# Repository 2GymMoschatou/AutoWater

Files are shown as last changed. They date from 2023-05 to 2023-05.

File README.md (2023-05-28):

# AutoWater
Σύστημα αυτόματου ποτίσματος τροφοδοτούμενου από δεξαμενή συλλογής νερού

Σχεδίαση, προγραμματισμός και κατασκευή μοντέλου επίδειξης ενός συστήματος αυτόματου ποτίσματος τροφοδοτούμενου από δεξαμενή συλλογής του νερού της βροχής.
Το σύστημα ανιχνεύει την υγρασία του εδάφους σε δύο σημεία (παρτέρια) και ανάλογα με το ποσοστό υγρασίας ποτίζει το ένα ή και τα δύο σημεία, ανεξάρτητα μεταξύ τους. Η διαδικασία του ποτίσματος πραγματοποιείται κατά τις βραδινές ώρες για να είναι πιο αποδοτική.
Το νερό για το πότισμα προέρχεται από δεξαμενή συγκέντρωσης των νερών της βροχής, η οποία ελέγχεται από αισθητήρα στάθμης του νερού. Αν η δεξαμενή είναι άδεια τα παρτέρια ποτίζονται από το δίκτυο ύδρευσης.
Η κατάσταση του συστήματος, καθώς και οι μετρήσεις υγρασίας και θερμοκρασίας του περιβάλλοντος προβάλλονται μέσω της θύρας USB σε υπολογιστή.

Υλικά και κόστος του συστήματος αυτόματου ποτίσματος
| Περιγραφή | Κόστος |
| --- | --- |
| Arduino Uno (συμβατό) | 9,90 € |
| Φωτοαντίσταση |	0,20 € |
| Αντίσταση 10ΚΩ | 0,02 € |
| Αισθητήρας υγρασίας εδάφους (2 τεμ) | 3,80 € |
| Αισθητήρας υπερήχων HC-SR04 |	2,50 € |
| Αισθητήρας υγρασίας και θερμοκρασίας DHT11 | 2,40 € |
| Servo Micro MG90 (3 τεμ) | 14,70 € |
| Αντλία υγρών 5V (2 τεμ) |	9,80 € |
| Σωλήνας σιλικόνης (6x8mm) 2μ | 2,40 € |
| Μονάδες ρελέ (2 τεμ) | 3,80 € |
| Μπαταριοθήκη 4ΑΑ | 0,60 € |
| Μπαταρίες ΑΑ (4 τεμ) | 1,80 € |
| Διακόπτης ON-ON | 0,80 € |
| Διάτρητη πλακέτα σε σχήμα breadboard | 3,80 € |
| Σύνολο | 56,52 € |

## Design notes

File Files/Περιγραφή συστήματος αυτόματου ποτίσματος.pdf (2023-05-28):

# Σύστημα αυτόματου ποτίσματος τροφοδοτούμενου από δεξαμενή συλλογής νερού

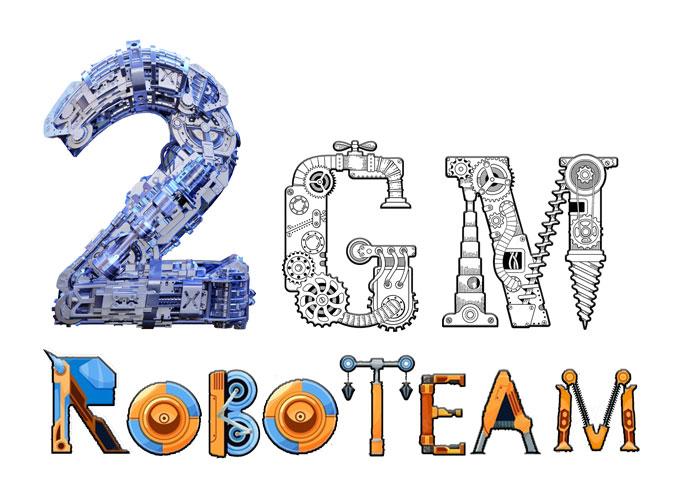
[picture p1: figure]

# 2ο Γυμνάσιο Μοσχάτου

# Σχολικό έτος 2022 - 23

## Η κατανομή των υδατικών πόρων στην Ελλάδα

Η χώρα μας διαθέτει συνολικά επαρκείς υδατικούς πόρους, επιφανειακούς και υπόγειους, αλλά η γεωμορφολογική της σύνθεση, η γεωλογική δομή, η άνιση κατανομή των βροχοπτώσεων στο χώρο και στο χρόνο και τέλος η άνιση κατανομή των δραστηριοτήτων, και επομένως των υδατικών αναγκών, κυρίως στο χώρο, μειώνουν σημαντικά τη διαθέσιμη ποσότητα και δυσκολεύουν την αξιοποίηση.
Τα ιδιαίτερα χαρακτηριστικά της χώρας, σε σχέση με τους υδατικούς πόρους, από τα οποία προκύπτουν και οι δυσκολίες διαχείρισής τους, μπορούν να ταξινομηθούν ως εξής :
- Ως προς την κατανομή των βροχοπτώσεων, η οποία είναι άνιση ως προς το χώρο και το χρόνο. Συγκεκριμένα η Δυτική Ελλάδα δέχεται μεγαλύτερα ύψη βροχών από ότι η Ανατολική.
- Ως προς την κατανομή της ζήτησης, η οποία είναι άνιση ως προς το χώρο και ως προς το χρόνο.
- Ως προς τη μορφολογία της επιφάνειας της χώρας, με τη δημιουργία πολλών μικρών υδάτινων ρευμάτων.
Σχετικά με την κατανομή των βροχών παρατηρούνται σημαντικές διαφοροποιήσεις από περιοχή σε περιοχή. Έτσι, στα νότια και τα νησιά το φθινόπωρο και το χειμώνα έχουμε το μέγιστο της βροχής, ενώ το καλοκαίρι και μέρος της άνοιξης επικρατεί σχεδόν ξηρασία. Στα βόρεια η χρονική αυτή κατανομή αλλάζει σημαντικά, όπου φθινόπωρο-χειμώνας-άνοιξη έχουν σχεδόν ισοκατανομή της βροχής, με το καλοκαίρι να παραμένει σχεδόν ξερό. Είναι φυσικό, ότι κάτω από αυτές τις συνθήκες, για να γίνει δυνατή η ανάπτυξη των καλλιεργειών από τα μέσα της άνοιξης μέχρι το τέλος τουλάχιστον του καλοκαιριού, χρειάζεται η εφαρμογή αρδεύσεων.

## Περιγραφή του συστήματος αυτόματου ποτίσματος

Παραδοσιακά σε περιοχές που
παρατηρείται μεγαλύτερη ξηρασία οι
κάτοικοι συγκέντρωναν το νερό της
βροχής σε στέρνες, όπως μας μαρτυρούν και λογοτεχνικές πηγές. Στο σύστημα αυτόματου ποτίσματος που σχεδιάσαμε συγκεντρώνουμε το νερό της βροχής σε δεξαμενή, από όπου ποτίζουμε τα φυτά που βρίσκονται σε δύο διαφορετικά παρτέρια.
Το σύστημά μας, ανιχνεύει την υγρασία του εδάφους σε δύο σημεία και ανάλογα με το ποσοστό υγρασίας ενεργοποιεί τις αντίστοιχες αντλίες για να τα ποτίσει. Η διαδικασία του ποτίσματος πραγματοποιείται τις βραδινές ώρες για να έχουμε μικρότερη εξάτμιση, επομένως να είναι πιο αποδοτική. Αν η δεξαμενή είναι
άδεια τα παρτέρια ποτίζονται από το
δίκτυο ύδρευσης.

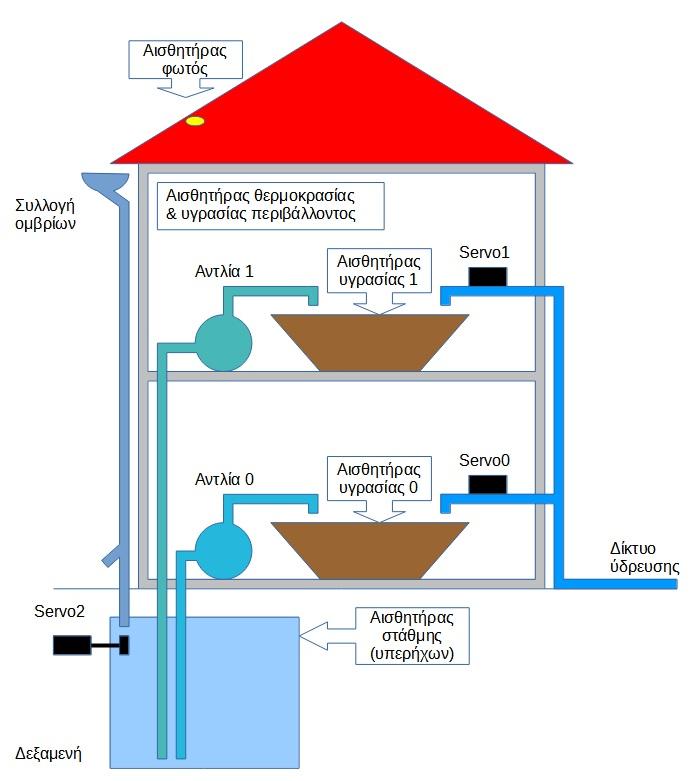
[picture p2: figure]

Για την προσομοίωση της λειτουργίας και του προγραμματισμού των επιμέρους στοιχείων, καθώς και του πλήρους συστήματος, πριν την τελική συναρμολόγηση, χρησιμοποιήθηκε το ελεύθερο λογισμικό TinkerCAD. Στο παρακάτω σχέδιο βλέπουμε το κύκλωμα, με το οποίο έγινε η προσομοίωση στο TinkerCAD.

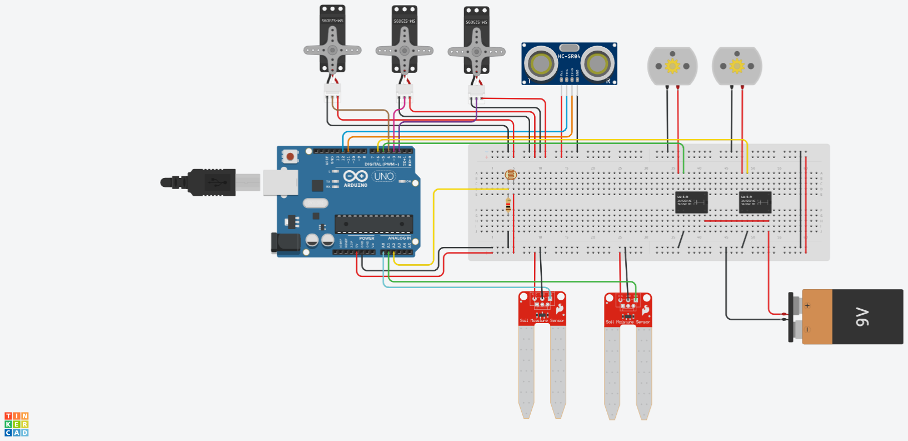
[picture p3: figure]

Στην τελική υλοποίηση τοποθετήθηκαν μονάδες ρελέ στη θέση των ρελέ που φαίνονται στο σχέδιο και ο αισθητήρας DHT11, τα οποία δεν υπάρχουν στο λογισμικό της προσομοίωσης.

Για την κατασκευή του συστήματος χρησιμοποιήσαμε:
Περιγραφή | Τεμάχια | Τιμή μονάδας | Κόστος
Arduino Uno SMD Compatible - CH340 | 1 | 9.90 € | 9.90 €
Φωτοαντίσταση LDR 5mm | 1 | 0.20 € | 0.20 €
Αντίσταση 10ΚΩ | 1 | 0,02 € | 0,02 €
Αισθητήρα υγρασίας εδάφους | 2 | 1,90 € | 3,80 €
Αισθητήρα υπερήχων HC-SR04 | 1 | 2.50 € | 2.50 €
Αισθητήρα υγρασίας και θερμοκρασίας DHT11 | 1 | 2,40 € | 2,40 €
Servo micro MG90S | 3 | 4,90 € | 14,70 €
Αντλίες υγρών 5V | 2 | 4,90 € | 9,80 €
Σωλήνας σιλικόνης (6x8mm) μ | 2 | 1,20 € | 2,40 €
Relay module - 1 channel 5V high level trigger | 2 | 1.90 € | 3,80 €
Μπαταριοθήκη 4ΑΑ με καλώδια | 1 | 0,60 € | 0,60 €
Μπαταρίες ΑΑ (4τεμ) | 1 | 1,80 € | 1,80 €
Διακόπτης ON-ON | 1 | 0,80 € | 0,80 €
Διάτρητη πλακέτα σε σχήμα breadboard | 1 | 3,80 € | 3,80 €
Συνολικό κόστος | | | 56,52 €
Στον παραπάνω πίνακα δεν περιλαμβάνεται το κόστος της καλωδίωσης, το οποίο εξαρτάται από το μέγεθος της μακέτας που θα κατασκευαστεί.

## Κατασκευή του μοντέλου επίδειξης

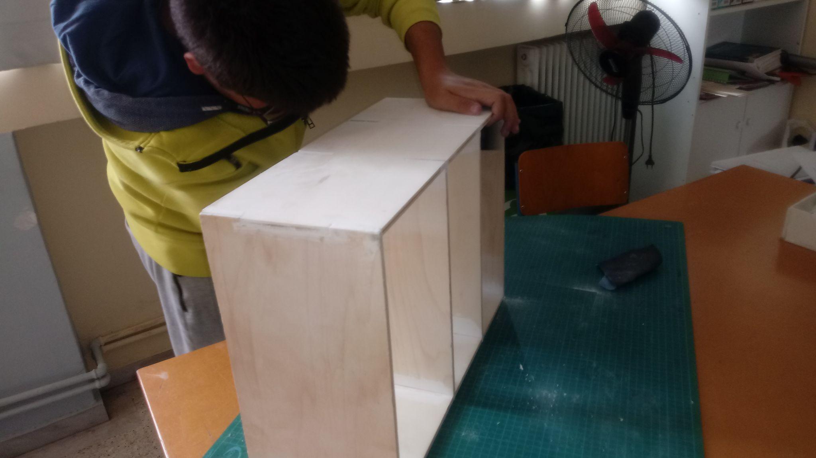
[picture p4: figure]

Για την επίδειξη της λειτουργίας του
συστήματος κατασκευάσαμε ένα ξύλινο
ομοίωμα σπιτιού με υπόγειο, ισόγειο και
πρώτο όροφο. Το ομοίωμα βάφτηκε με λευκό χρώμα στους δύο ορόφους και γκρι στο υπόγειο.

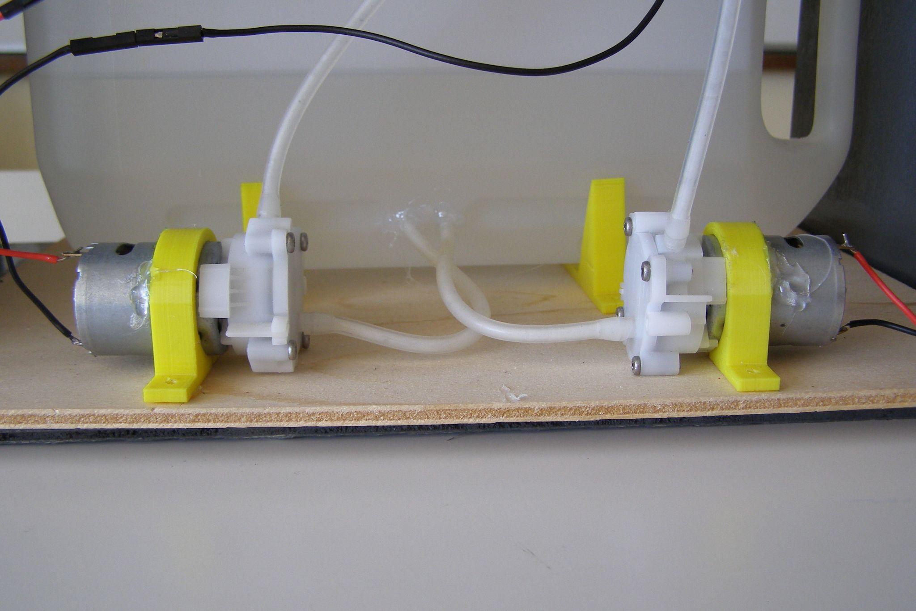
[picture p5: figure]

Στο υπόγειο του κτιρίου τοποθετήσαμε τις αντλίες του συστήματος και ένα πλαστικό δοχείο για δεξαμενή, στο οποίο ανοίξαμε τις υποδοχές για τις απαραίτητες σωληνώσεις.

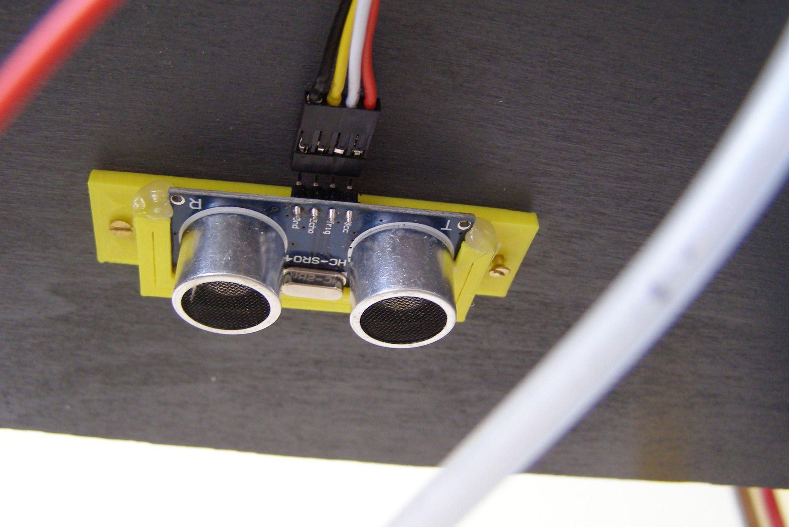
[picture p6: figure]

Ο αισθητήρας υπερήχων τοποθετήθηκε στην οροφή του υπογείου και ανιχνεύει το ύψος του νερού της δεξαμενής από το αντίστοιχο άνοιγμα στο δοχείο.

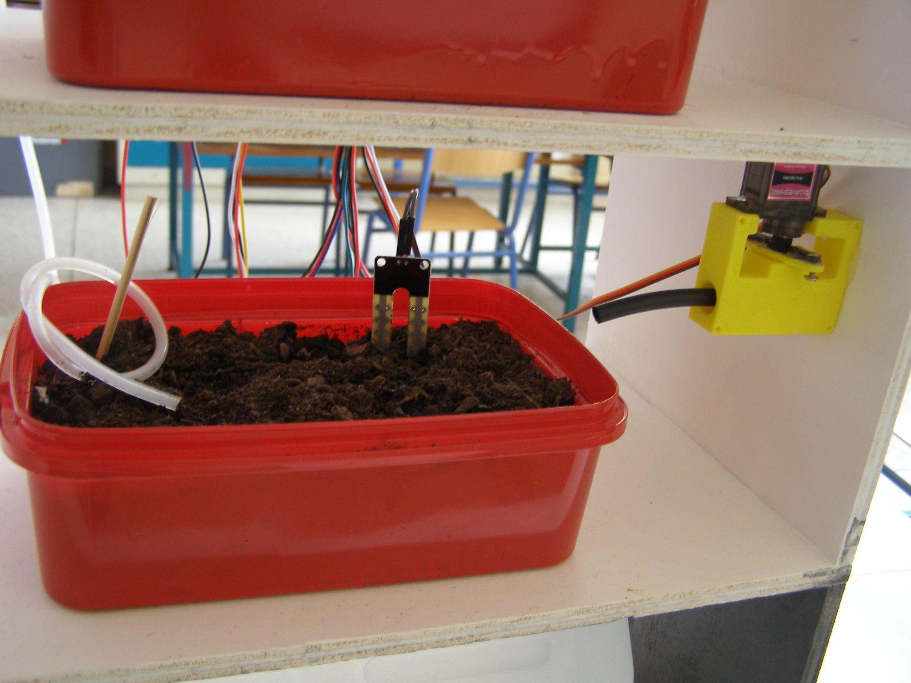
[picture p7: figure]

Στους ορόφους του κτιρίου τοποθετήσαμε πλαστικά δοχεία με χώμα για τα παρτέρια, όπου βάλαμε τους αισθητήρες υγρασίας εδάφους. Σε κάθε όροφο έχουμε και ένα διακόπτη για το νερό του δικτύου ύδρευσης ελεγχόμενο από servo.

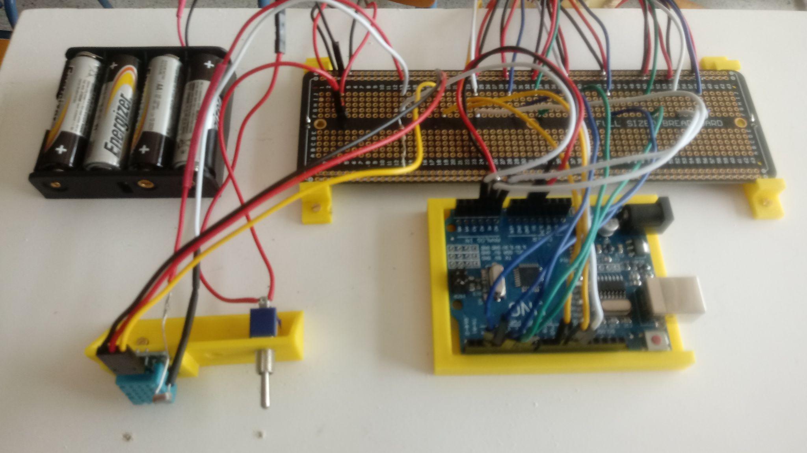
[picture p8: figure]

Στο πάνω μέρος του ομοιώματος τοποθετήσαμε την πλακέτα του Arduino Uno και την πλακέτα στην οποία καταλήγουν όλες οι καλωδιώσεις του συστήματος. Επίσης, τοποθετήσαμε τον αισθητήρα θερμοκρασίας-υγρασίας, τη φωτοαντίσταση και τις μπαταρίες τροφοδοσίας των αντλιών με το διακόπτη τους

Η σκεπή του ομοιώματος κατασκευάστηκε από διαφανές plexiglass.

Στο εξωτερικό μέρος τοποθετήθηκε ομοίωμα της υδρορροής με ένα διακόπτη ελεγχόμενο από servo για τον έλεγχο της παροχής νερού στη δεξαμενή.

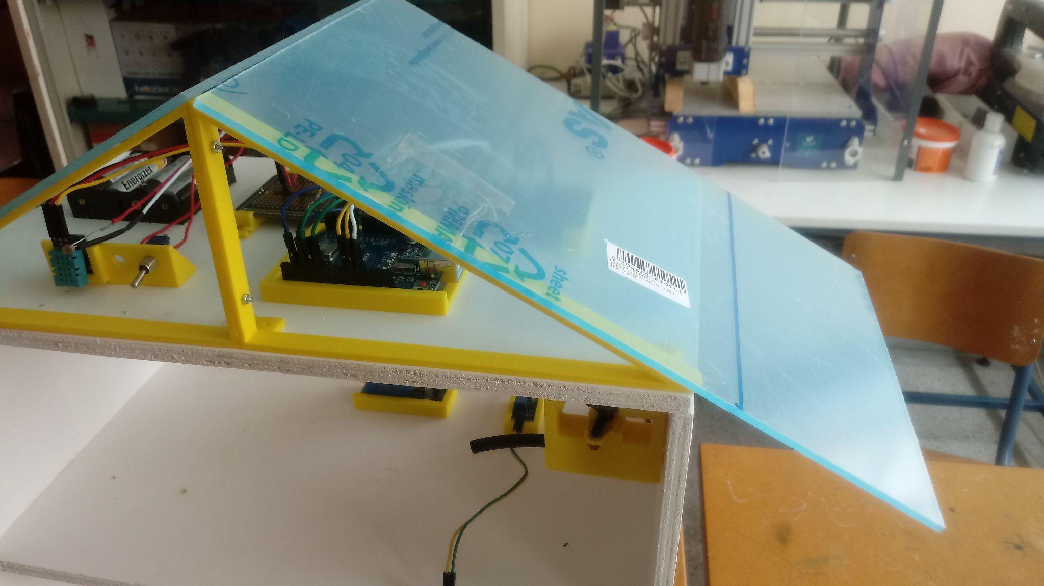
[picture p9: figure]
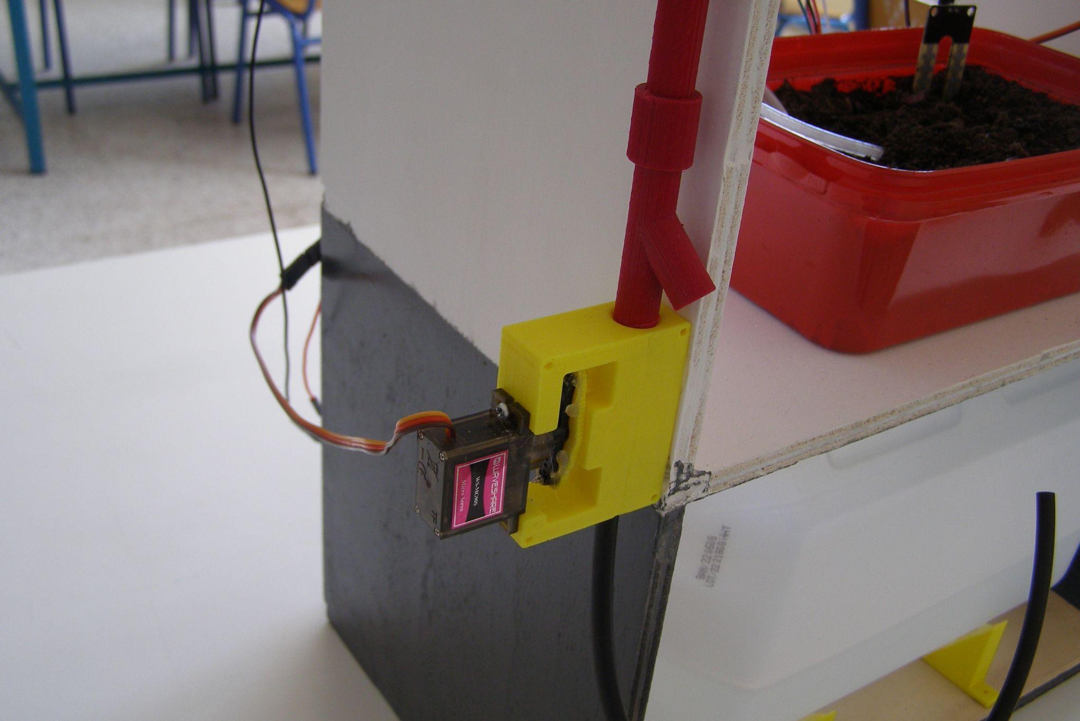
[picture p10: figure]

Οι βάσεις για τους αισθητήρες και τα υπόλοιπα στοιχεία του συστήματος, καθώς και η βάση της στέγης και η υδρορροή, σχεδιάστηκαν με το πρόγραμμα TinkerCAD και εκτυπώθηκαν με τον 3D printer, ενώ για τους διακόπτες νερού χρησιμοποιήθηκε ελεύθερο σχέδιο από την ιστοσελίδα Thingiverse.com (https://www.thingiverse.com/thing:1624066).
Η μακέτα του συστήματος ολοκληρωμένη
φαίνεται στην παρακάτω φωτογραφία.

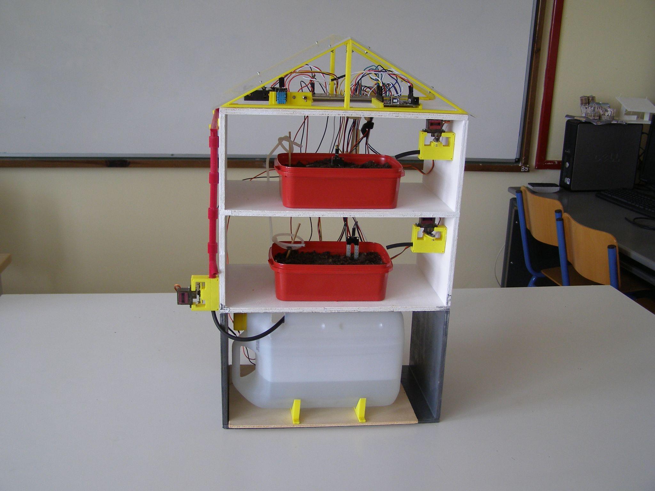
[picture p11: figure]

## Προγραμματισμός του συστήματος αυτόματου ποτίσματος

Για τον προγραμματισμό του συστήματος χρησιμοποιήθηκε το λογισμικό Arduino IDE.
Ένα απλό πρόγραμμα που επαναλαμβάνεται στο Arduino αποτελείται από δύο συναρτήσεις: •Τη συνάρτηση setup(), που εκτελείται μόνο μια φορά στην αρχή του προγράμματος, και καθορίζει τις αρχικές ρυθμίσεις του συστήματος.
•Τη συνάρτηση loop(), που περιέχει τον κυρίως κώδικα του προγράμματός μας, και εκτελείται κυκλικά μέχρι την απενεργοποίηση ή την επανεκκίνηση του Arduino.

Στο πρώτο μέρος του προγράμματός μας εισάγουμε τις απαραίτητες βιβλιοθήκες για την εκτέλεσή του και δημιουργούμε τα αντικείμενα των servo που χρειαζόμαστε, ορίζοντας και τις αρχικές τους θέσεις.

//Including libraries
#include <Servo.h>

#include <DHT.h>

//Creating servos and setting initial positions Servo servo0;
Servo servo1;
Servo servo2;
int servo0Pos = 90;
int servo1Pos = 90;
int servo2Pos = 0;

Έπειτα ορίζουμε τους ακροδέκτες όπου θα συνδεθούν τα servo, τα ρελέ και οι αισθητήρες του κυκλώματος.

//Setting pins
const int servo0Pin=2;
const int servo1Pin=3;
const int servo2Pin=4;
const int relay0Pin=5;
const int relay1Pin=6;
const int dhtPin=10;
const int echoPin=11;
const int trigPin=12;
const int hygro0Pin=A0;
const int hygro1Pin=A1;
const int lightPin=A2;

Επίσης ορίζουμε το όνομα και τον τύπο των μεταβλητών, καθώς και τον τύπο του αισθητήρα DHT που θα χρησιμοποιήσουμε.

//Setting the variables
int hygro0;
int hygro1;
int light;

long duration;
long distance;
bool water0;
bool water1;
float hum;
float temp;

//Setting the DHT sensor type
#define dhtType DHT11

DHT dht(dhtPin, dhtType);

Τέλος καθορίζουμε τις τιμές των μεταβλητών, όπου θα λαμβάνονται οι κρίσιμες αποφάσεις, ώστε, σε περίπτωση αλλαγής των ορίων λειτουργίας της δεξαμενής για παράδειγμα, να τροποποιούνται οι τιμές μόνο μια φορά και όχι σε όποιο σημείο του προγράμματος πρέπει να πάρουμε μια απόφαση.

//Setting the critical values
const int minDistance=5;
const int maxDistance=10;
const int minLight=15;

Στην ενότητα setup, πρώτα ενεργοποιούμε την σειριακή θύρα του Arduino και τον αισθητήρα υγρασίας-θερμοκρασίας DHT11. Στη συνέχεια συνδέουμε τα Servo με τους αντίστοιχους ακροδέκτες και τα τοποθετούμε στην αρχική τους θέση. Τέλος καθορίζουμε τον τρόπο λειτουργίας των ψηφιακών ακροδεκτών που έχουμε ορίσει ότι θα χρησιμοποιήσουμε.

void setup() {
//Initialize serial communication and DHT sensor
Serial.begin(9600);
dht.begin();

//Attaching servos and writing initial positions servo0.attach(servo0Pin);
servo1.attach(servo1Pin);
servo2.attach(servo2Pin);
servo0.write(servo0Pos);
servo1.write(servo1Pos);
servo2.write(servo2Pos);

//Initialize digital pins
pinMode(relay0Pin, OUTPUT); pinMode(relay1Pin, OUTPUT); pinMode(trigPin, OUTPUT);
pinMode(echoPin, INPUT);

}

Στην ενότητα loop ξεκινάμε με την ανάγνωση των ενδείξεων από τους αισθητήρες του συστήματος, δηλαδή το ύψος της δεξαμενής νερού, την υγρασία του εδάφους στα παρτέρια και την φωτεινότητα.

void loop() {
//Read water level with ultrasonic sensor
digitalWrite(trigPin, LOW); delayMicroseconds(2);
digitalWrite(trigPin, HIGH); delayMicroseconds(10);
digitalWrite(trigPin, LOW); duration = pulseIn(echoPin, HIGH); distance = (duration/2) / 29.1; delay(100);

//Read moisture of plants at floor 0 hygro0 = analogRead(hygro0Pin); hygro0 = constrain(hygro0,400,1023); hygro0 = map(hygro0,400,1023,100,0); delay(100);

//Read moisture of plants at floor 1 hygro1 = analogRead(hygro1Pin); hygro1 = constrain(hygro1,400,1023); hygro1 = map(hygro1,400,1023,100,0); delay(100);

//Read light
light = analogRead(lightPin);
delay(100);

//Reading environment temperature and humidity
//Reading temperature or humidity takes about 250 milliseconds! hum = dht.readHumidity();
temp = dht.readTemperature();
delay(250);

Ελέγχουμε στη συνέχεια το ύψος του νερού στη δεξαμενή και, στην περίπτωση που ανιχνεύσουμε το ελάχιστο όριο που έχουμε θέσει, διακόπτουμε την παροχή νερού από την υδρορροή, για να αποφύγουμε την υπερχείλιση της δεξαμενής.

//Check tank overflow
if (distance<=minDistance){
servo2Pos=90;
servo2.write(servo2Pos);
delay(100);
}
else{

servo2Pos=0;
servo2.write(servo2Pos);
delay(100);
}

Μετά ελέγχουμε την υγρασία του πρώτου παρτεριού και καθορίζουμε αν τα φυτά χρειάζονται πότισμα.

//Check plants in floor 0
if (light<minLight){
if (hygro0<30){
water0=true;
}
}
if (hygro0>90){
water0=false;
}

Αν τα φυτά μας πρέπει να ποτιστούν, ελέγχουμε αν η δεξαμενή έχει νερό και ενεργοποιούμε την αντίστοιχη αντλία. Στην περίπτωση που η δεξαμενή δεν έχει νερό ανοίγουμε το δίκτυο ύδρευσης.

//Watering plants in floor 0
if (water0==true){
if (distance<maxDistance){ digitalWrite(relay0Pin, HIGH); delay(100);
servo0Pos=90;
servo0.write(servo0Pos);
delay(100);
}
else{
digitalWrite(relay0Pin, LOW); delay(100);
servo0Pos=0;
servo0.write(servo0Pos);
delay(100);
}
}

Επαναλαμβάνουμε τη ίδια διαδικασία και για το δεύτερο παρτέρι.

//Check plants in floor 1
if (light<minLight){
if (hygro1<30){
water1=true;
}
}

if (hygro1>90){
water1=false;
}

//Watering plants in floor 1
if (water1==true){
if (distance<maxDistance){ digitalWrite(relay1Pin, HIGH); delay(100);
servo1Pos=90;
servo1.write(servo1Pos);
delay(100);
}
else{
digitalWrite(relay1Pin, LOW); delay(100);
servo1Pos=0;
servo1.write(servo1Pos);
delay(100);
}
}

Όταν η υγρασία του εδάφους φτάσει στην τιμή που έχουμε καθορίσει, τότε το πότισμα στο αντίστοιχο παρτέρι διακόπτεται.

//Stop watering in floor 0
if (water0==false){
digitalWrite(relay0Pin, LOW); delay(100);
servo0Pos=90;
servo0.write(servo0Pos);
delay(100);
}

//Stop watering in floor 1
if (water1==false){
digitalWrite(relay1Pin, LOW); delay(100);
servo1Pos=90;
servo1.write(servo1Pos);
delay(100);
}

Στο τέλος της ενότητας οι ενδείξεις των αισθητήρων διαβιβάζονται στον συνδεδεμένο υπολογιστή μέσω της σειριακής θύρας του Arduino.

//Print out the values
Serial.print("Water depth ");

Serial.print(distance);
Serial.println(" cm");
Serial.print("Soil humidity 0: "); Serial.print(hygro0);
Serial.println("%");
Serial.print("Soil humidity 1: "); Serial.print(hygro1);
Serial.println("%");
Serial.print("Light: ");
Serial.println(light);
Serial.print("Environment Humidity: "); Serial.print(hum);
Serial.println("%");
Serial.print("Environment Temperature: ");
Serial.print(temp);
Serial.println("°C ");

Ακολουθεί μια παύση ενός δευτερολέπτου για το κλείσιμο της ενότητας και την εκτέλεσή της από την αρχή.

delay(1000);
}

## Βιβλιογραφία

1. Γ. Βούτσινος, Γ. Καλκάνης, Κ. Κοσμάς, Κ. Σούτσας, “Γεωλογία & Διαχείριση Φυσικών Πόρων”, Ινστιτούτο Τεχνολογίας Υπολογιστών & Εκδόσεων «Διόφαντος» (http://ebooks.edu.gr/ebooks/v/html/8547/2690/Geologia-kai-Diacheirisi-Fysikon-Poron-A-Lykeiou_html-apli/index.html)
2. Βασίλης Νούσης, “ARDUINO για αρχάριους”, 2019 (http://3gym-igoum.thesp.sch.gr/images/Arduino/book.pdf)
3. Εμμανουήλ Πουλάκης, “Προγραμματίζοντας με τον μικροελεγκτή Arduino”, 2015 (https://www.openbook.gr/programmatizontas-me-ton-mikroelegkti-arduino/)

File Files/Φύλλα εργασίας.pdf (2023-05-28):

# Σύστημα αυτόματου ποτίσματος τροφοδοτούμενου από δεξαμενή συλλογής νερού


# Φύλλα εργασίας

# 2ο Γυμνάσιο Μοσχάτου

# Σχολικό έτος 2022 - 23

## Εισαγωγή

Τα φύλλα εργασίας που περιλαμβάνονται στις παρούσες σημειώσεις εξηγούν τη λειτουργία και τη χρήση των επιμέρους στοιχείων που χρησιμοποιούμε στο σύστημα αυτόματου ποτίσματος. Η εκτέλεση των δραστηριοτήτων μπορεί να γίνει εξ ολοκλήρου στο ελεύθερο λογισμικό TinkerCAD και δεν απαιτείται η αγορά εξοπλισμού.

## Φύλλο εργασίας 1 - Μελέτη αισθητήρα υπερήχων

Ο αισθητήρας υπερήχων χρησιμοποιεί ήχο πάνω από την μέγιστη συχνότητα ακοής για να ανιχνεύσει απόσταση. Ο αισθητήρας εκπέμπει ένα σύντομο παλμό ήχου και περιμένει να επιστρέψει. Μετρά τον χρόνο που χρειάζεται για να ταξιδέψει ο ήχος, να ανακλαστεί σε ένα αντικείμενο και μετά να επιστρέψει στον αισθητήρα. Επειδή η ταχύτητα του ήχου είναι γνωστή, ο συνολικός χρόνος που απαιτείται για την επιστροφή του ήχου εξαρτάται από την απόσταση του αντικειμένου.

Α. Μέτρηση απόστασης με τον αισθητήρα υπερήχων

Σχεδιάζουμε το παρακάτω κύκλωμα στο TINKERCAD:

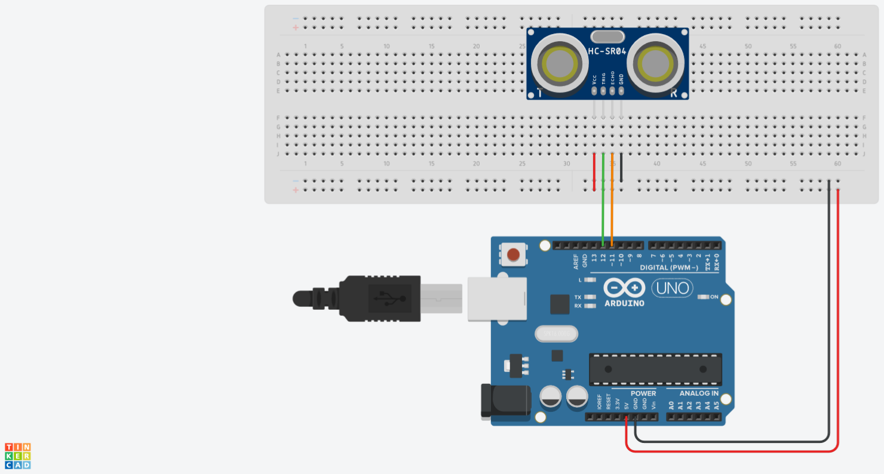
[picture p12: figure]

Εισάγουμε τον παρακάτω κώδικα: const int echoPin=11;
const int trigPin=12;
long duration;
long distance;

void setup() {
Serial.begin(9600);
pinMode(trigPin, OUTPUT);
pinMode(echoPin, INPUT);
}

void loop() {
digitalWrite(trigPin, LOW); delayMicroseconds(2);
digitalWrite(trigPin, HIGH); delayMicroseconds(10);
digitalWrite(trigPin, LOW); duration = pulseIn(echoPin, HIGH); distance = (duration/2) / 29.1;

Serial.print(distance);
Serial.println(" cm");
delay(1000);
}

Το πρόγραμμα διαβάζει την απόσταση ενός εμποδίου από τον αισθητήρα υπερήχων και καταγράφει την ένδειξη σε εκατοστά στη σειριακή.

Ξεκινάμε την προσομοίωση του κυκλώματος στο TinkerCAD.

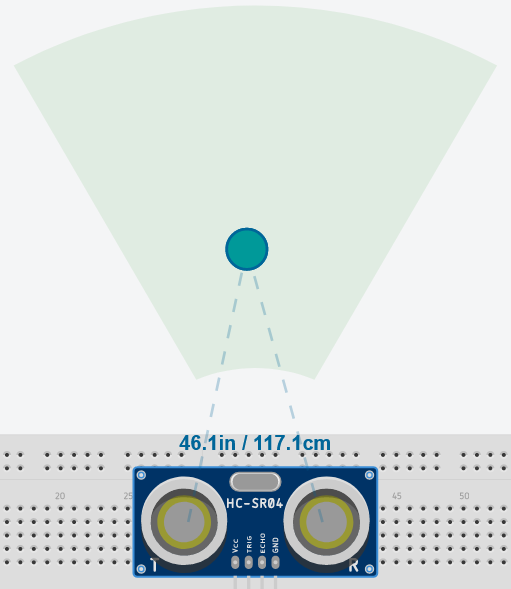
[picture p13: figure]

Επιλέγουμε τον αισθητήρα υπερήχων στον χώρο σχεδίασης και μεταβάλλουμε τη θέση του αντικειμένου:

Παρατηρούμε την ένδειξη στη σειριακή:

Β. Λήψη απόφασης ανάλογα με την απόσταση

Τροποποιούμε το προηγούμενο κύκλωμα στο TINKERCAD, όπως φαίνεται παρακάτω:

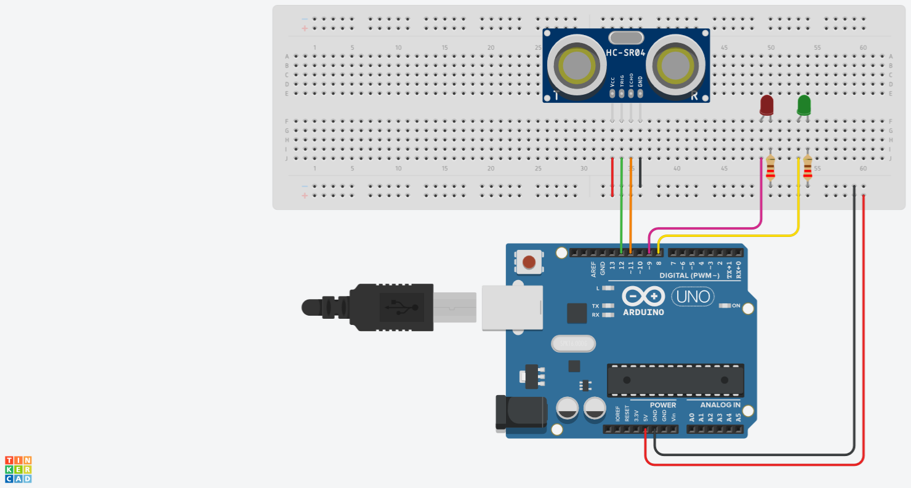
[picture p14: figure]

Τροποποιούμε το πρόγραμμα όπως φαίνεται παρακάτω:

const int ledGreen=8;
const int ledRed=9;
const int echoPin=11;
const int trigPin=12;
long duration;
long distance;

void setup() {
Serial.begin(9600);
pinMode(ledGreen, OUTPUT); pinMode(ledRed, OUTPUT);
pinMode(trigPin, OUTPUT);
pinMode(echoPin, INPUT);
}

void loop() {
digitalWrite(trigPin, LOW); delayMicroseconds(2);
digitalWrite(trigPin, HIGH); delayMicroseconds(10);
digitalWrite(trigPin, LOW); duration = pulseIn(echoPin, HIGH); distance = (duration/2) / 29.1;

if (distance<=30){
digitalWrite(ledRed, HIGH); digitalWrite(ledGreen, LOW); delay(100);
}
else{
digitalWrite(ledGreen, HIGH); digitalWrite(ledRed, LOW); delay(100);
}

Serial.print(distance);
Serial.println(" cm");
delay(1000);
}

Το πρόγραμμα διαβάζει την απόσταση ενός εμποδίου από τον αισθητήρα υπερήχων και ανάβει το κόκκινο LED αν η απόσταση είναι μικρότερη από 30 cm, ενώ ανάβει το πράσινο LED αν είναι μεγαλύτερη. Η απόσταση καταγράφεται σε εκατοστά και στη σειριακή.

Ξεκινάμε την προσομοίωση του κυκλώματος στο TinkerCAD.
Επιλέγουμε τον αισθητήρα υπερήχων στον χώρο σχεδίασης και μεταβάλλουμε τη θέση του αντικειμένου.

Ελέγχουμε τη σωστή εκτέλεση του προγράμματος παρατηρώντας τις ενδείξεις των LEDs και της σειριακής.

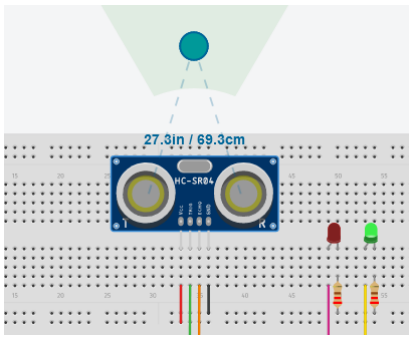
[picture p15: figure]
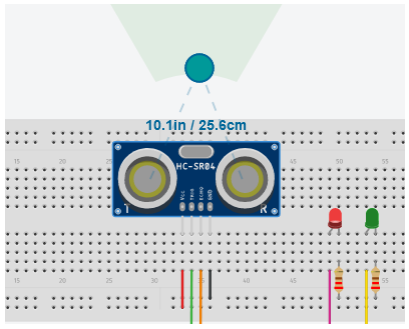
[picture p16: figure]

## Φύλλο εργασίας 2 - Μέτρηση αναλογικών μεγεθών

Για να μετρήσουμε αναλογικά μεγέθη με το Arduino Uno χρησιμοποιούμε τις αναλογικές θύρες Α0 μέχρι Α5. Οι αναλογικές θύρες είναι συνδεδεμένες, μέσω ενός πολυπλέκτη, σε ένα μετατροπέα αναλογικού σε ψηφιακό (ADC). Ο μετατροπέας αναλογικού σε ψηφιακό μπορεί να μετατρέψει μια τιμή αναλογικού σήματος σε ψηφιακή αναπαράσταση. Στο Arduino Uno ο μετατροπέας αναλογικού σε ψηφιακό έχει ανάλυση 10-bit. Αυτό σημαίνει ότι μια τάση μεταξύ 0 και 5V σε μια αναλογική θύρα του Arduino Uno θα αντιπροσωπεύεται από μια αντίστοιχη τιμή μεταξύ 0 και 1023. Το αποτέλεσμα μιας αναλογικο-ψηφιακής μετατροπής σε κάποια αναλογική είσοδο του Arduino μπορούμε να "διαβάσουμε" με την εντολή analogRead().

Α. Ανάγνωση αναλογικής εισόδου

Σχεδιάζουμε το παρακάτω κύκλωμα στο TINKERCAD:

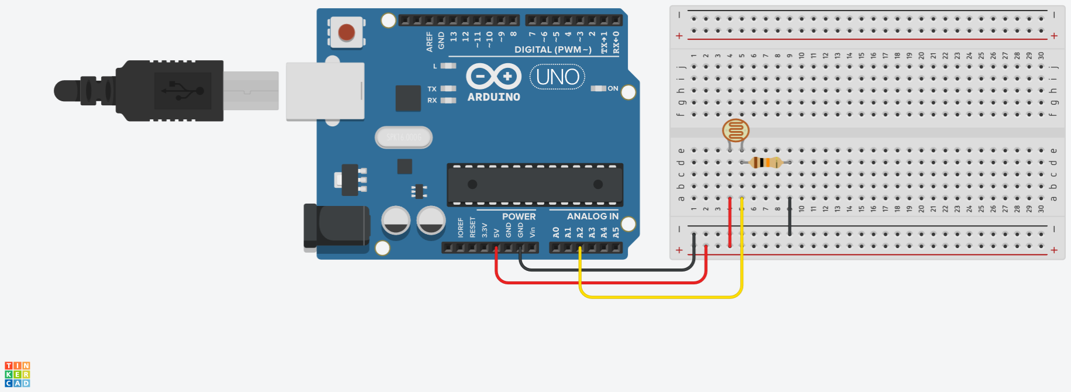
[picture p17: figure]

Εισάγουμε τον παρακάτω κώδικα: const int lightPin=A2;
int light;

void setup() {
Serial.begin(9600);
}

void loop() {
light = analogRead(lightPin); delay(100);

Serial.print("Light: ");
Serial.println(light);
}

Στο κύκλωμα χρησιμοποιούμε μια φωτοαντίσταση σε συνδεσμολογία διαιρέτη τάσης με μια αντίσταση σταθερής τιμής 10kΩ. Το πρόγραμμα διαβάζει την τιμή της τάσης στα άκρα της αντίστασης των 10kΩ και καταγράφει την ένδειξη του μετατροπέα αναλογικού σε ψηφιακό στη σειριακή.

Ξεκινάμε την προσομοίωση του κυκλώματος στο TinkerCAD.

Επιλέγουμε τη φωτοαντίσταση στον χώρο σχεδίασης και μεταβάλλουμε τη θέση του δρομέα:

Παρατηρούμε την ένδειξη στη σειριακή:

Β. Αναγωγή αναλογικής εισόδου σε ποσοστό %

Σχεδιάζουμε το παρακάτω κύκλωμα στο TINKERCAD:

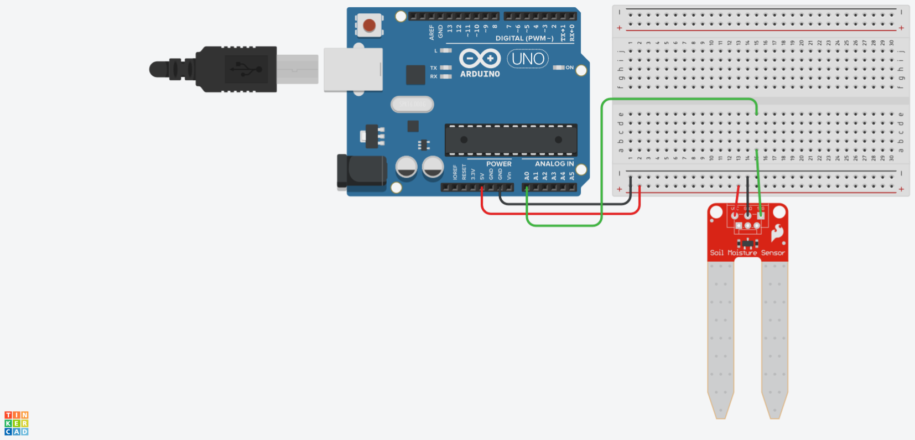
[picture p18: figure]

Εισάγουμε τον παρακάτω κώδικα: const int hygro0Pin=A0;
int hygro0;

void setup() {
Serial.begin(9600);
}

void loop() {
hygro0 = analogRead(hygro0Pin); hygro0 = constrain(hygro0,400,1023); hygro0 = map(hygro0,400,1023,100,0); delay(100);

Serial.print("Soil humidity 0: "); Serial.print(hygro0);
Serial.println("%");
}

Τα δύο άκρα του αισθητήρα υγρασίας εδάφους λειτουργούν ως μεταβλητή αντίσταση. Περισσότερο νερό στο έδαφος σημαίνει καλύτερη αγωγιμότητα, επομένως μικρότερη αντίσταση. Όταν η υγρασία είναι μέγιστη, ο αισθητήρας δίνει μια τιμή μεταξύ 300 και 400. Με την εντολή constrain() θέτουμε το ελάχιστο όριο της μέτρησης, ενώ με την εντολή map() εκφράζουμε τις μετρήσεις σε ποσοστό με την μικρότερη μέτρηση να αντιστοιχεί στο μέγιστο ποσοστό υγρασίας. Το ποσοστό της υγρασίας καταγράφεται στη σειριακή.

Ξεκινάμε την προσομοίωση του κυκλώματος στο TinkerCAD.

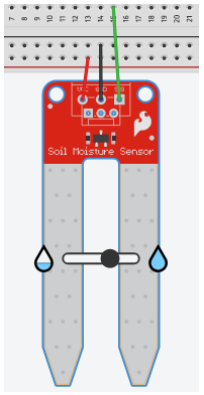
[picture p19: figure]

Επιλέγουμε τον αισθητήρα υγρασίας στο χώρο σχεδίασης και μεταβάλλουμε τη θέση του δρομέα:

Παρατηρούμε την ένδειξη στη σειριακή:

## Φύλλο εργασίας 3 - Χειρισμός servo

Ένα servo είναι μια διάταξη που αποτελείται από ένα μικρό ηλεκτρικό κινητήρα, ένα συνδυασμό γραναζιών και ένα σύστημα για τον ακριβή έλεγχο της θέσης του άξονά του. Ο άξονας μπορεί να περιστρέφεται με μικρή ταχύτητα αλλά με μεγάλη ροπή με το εύρος περιστροφής να περιορίζεται μεταξύ 0 και 180 μοιρών (μισή περιστροφή).
Για να δουλέψει ένα servo, πρέπει να εισαχθεί η αντίστοιχη βιβλιοθήκη στο πρόγραμμα (#include <Servo.h>), να οριστεί μια μεταβλητή τύπου servo (servo myservo;) και ο ακροδέκτης μέσω του οποίου θα το χειριστούμε (int servoPin = 4;). Στη συνάρτηση setup() πρέπει να συσχετίσουμε τον ακροδέκτη με το σερβοκινητήρα (myservo.attach(servoPin);).

Α. Περιστροφή του servo

Σχεδιάζουμε το παρακάτω κύκλωμα στο TINKERCAD:

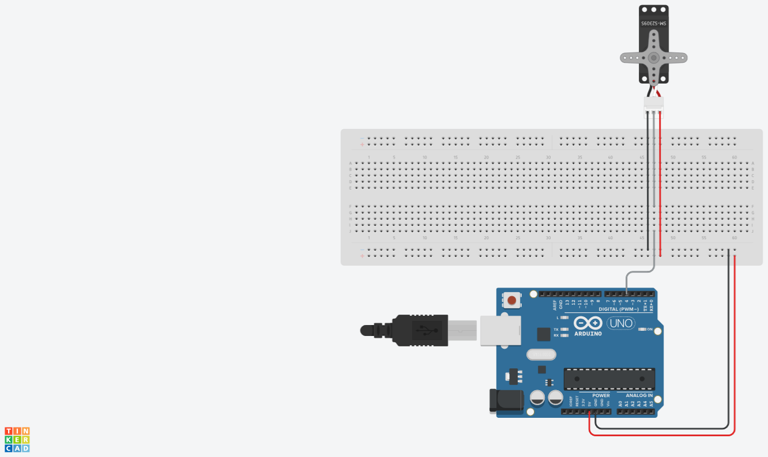
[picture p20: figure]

Εισάγουμε τον παρακάτω κώδικα: #include <Servo.h>

Servo servo2;
int servo2Pos = 0;
const int servo2Pin=4;

void setup() {
Serial.begin(9600);
servo2.attach(servo2Pin);
}

void loop() {
for (servo2Pos = 0; servo2Pos <= 180; servo2Pos += 30) { servo2.write(servo2Pos);
Serial.println(servo2Pos);
delay(500);
}
for (servo2Pos = 180; servo2Pos >= 0; servo2Pos -= 30) {

servo2.write(servo2Pos);
Serial.println(servo2Pos); delay(500);
}
}

Το πρόγραμμα περιστρέφει τον άξονα του servo από 0 μέχρι 180 μοίρες και αντίστροφα σε βήματα των 30 μοιρών.
Ξεκινάμε την προσομοίωση του κυκλώματος στο TinkerCAD και παρατηρούμε την περιστροφή του άξονα.

Β. Χειρισμός του servo με τον αισθητήρα υπερήχων.

Σχεδιάζουμε το παρακάτω κύκλωμα στο TINKERCAD:

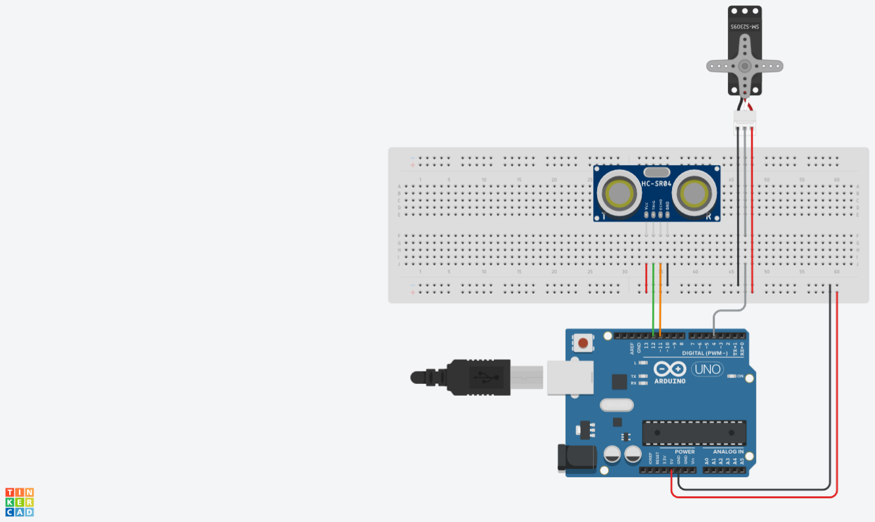
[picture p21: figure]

Εισάγουμε τον παρακάτω κώδικα: #include <Servo.h>

Servo servo2;
int servo2Pos = 0;

const int servo2Pin=4;
const int echoPin=11;
const int trigPin=12;
long duration;
long distance;

const int minDistance=30;

void setup() {
Serial.begin(9600);
servo2.attach(servo2Pin);
servo2.write(servo2Pos);
pinMode(trigPin, OUTPUT);

pinMode(echoPin, INPUT);
}

void loop() {
digitalWrite(trigPin, LOW); delayMicroseconds(2);
digitalWrite(trigPin, HIGH); delayMicroseconds(10);
digitalWrite(trigPin, LOW); duration = pulseIn(echoPin, HIGH); distance = (duration/2) / 29.1;

if (distance<=minDistance){ servo2Pos=90;
servo2.write(servo2Pos);
delay(100);
}
else{
servo2Pos=0;
servo2.write(servo2Pos);
delay(100);
}

Serial.print(distance);
Serial.println(" cm");
delay(1000);
}

Το πρόγραμμα περιστρέφει τον άξονα του servo από τις 0 στις 90 μοίρες, όταν η απόσταση που ανιχνεύει ο αισθητήρας υπερήχων είναι μικρότερη από 30 cm.

Ξεκινάμε την προσομοίωση του κυκλώματος στο TinkerCAD.

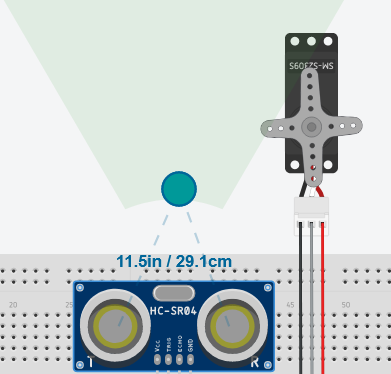
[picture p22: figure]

Επιλέγουμε τον αισθητήρα υπερήχων στο χώρο
σχεδίασης και μεταβάλλουμε τη θέση του αντικειμένου. Ελέγχουμε τη σωστή εκτέλεση του προγράμματος παρατηρώντας την περιστροφή του άξονα του servo.

## Φύλλο εργασίας 4 - Χειρισμός κινητήρων με τη βοήθεια ρελέ

Ο ηλεκτρονόμος ή ρελέ (relay) είναι μια ηλεκτρομηχανική διάταξη που λειτουργεί ως διακόπτης ελεγχόμενος από τάση.
Στην απλούστερη μορφή του πρόκειται για ένα διακόπτη που ενεργοποιείται με τη βοήθεια ενός ηλεκτρομαγνήτη. Όταν ο ηλεκτρομαγνήτης δεν διαρρέεται από ρεύμα είναι βραχυκυκλωμένες οι επαφές C (COMMON) και NC (Normal Closed) του διακόπτη, ενώ όταν ο ηλεκτρομαγνήτης διαρρέεται από ρεύμα βραχυκυκλώνονται οι επαφές C και NΟ (Normal Opened). Αφήνοντας την επαφή NC χωρίς σύνδεση, μπορούμε να συνδέσουμε το ρελέ ως απλό (on-off) διακόπτη σε ένα ηλεκτρικό κύκλωμα, που μπορεί να λειτουργήσει σε τάσεις μέχρι 250 V AC και ρεύματα μέχρι και 10 Α.
Σε μονάδες (module) ρελέ η ενεργοποίηση του ηλεκτρομαγνήτη γίνεται μέσω μιας ακίδας του (Signal ή Input), που συνδέεται σε μια ψηφιακή έξοδο του Arduino. Λογικό 1 στην ακίδα Signal ενεργοποιεί τον ηλεκτρομαγνήτη, και λογικό μηδέν τον απενεργοποιεί.
A. Ενεργοποίηση και απενεργοποίηση κινητήρα με τη βοήθεια ρελέ

Σχεδιάζουμε το παρακάτω κύκλωμα στο TINKERCAD:

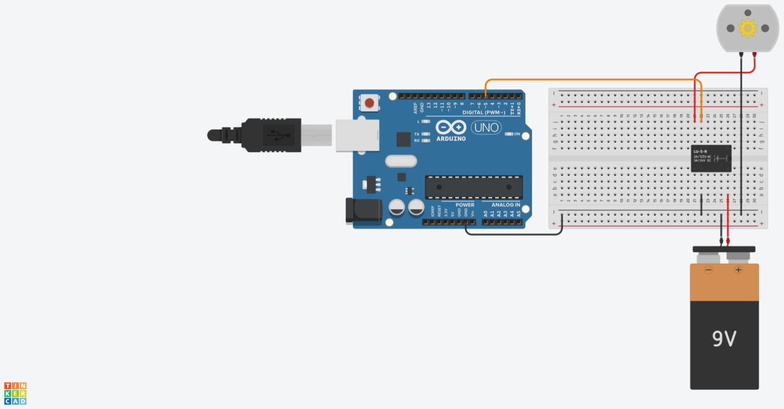
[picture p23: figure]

Εισάγουμε τον παρακάτω κώδικα: const int relay0Pin=5;

void setup() {
pinMode(relay0Pin, OUTPUT); }

void loop() {
digitalWrite(relay0Pin, HIGH); delay(3000);
digitalWrite(relay0Pin, LOW); delay(3000);

}

Το πρόγραμμα ενεργοποιεί τον κινητήρα για 3 δευτερόλεπτα και στη συνέχεια τον απενεργοποιεί για άλλα 3.
Ξεκινάμε την προσομοίωση του κυκλώματος στο TinkerCAD και παρατηρούμε τη λειτουργία του κινητήρα.

Β. Ενεργοποίηση κινητήρα με τον αισθητήρα υγρασίας

Σχεδιάζουμε το παρακάτω κύκλωμα στο TINKERCAD:

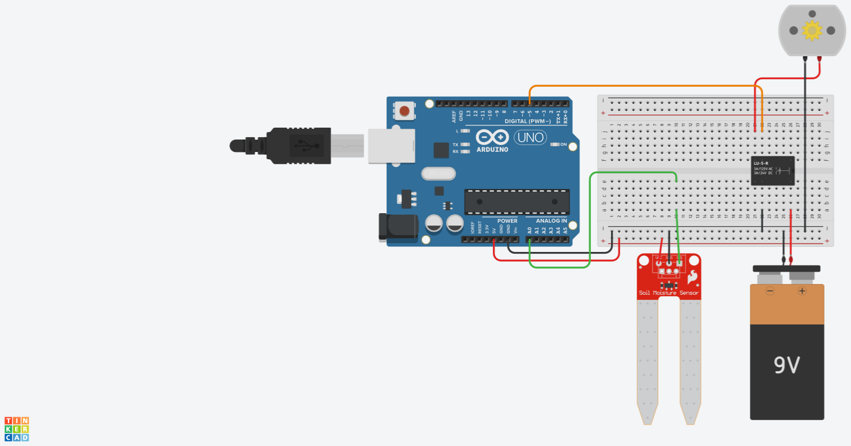
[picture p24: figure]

Εισάγουμε τον παρακάτω κώδικα: const int relay0Pin=5;
const int hygro0Pin=A0;
int hygro0;

void setup() {
Serial.begin(9600);
pinMode(relay0Pin, OUTPUT); }

void loop() {
hygro0 = analogRead(hygro0Pin); hygro0 = constrain(hygro0,400,1023); hygro0 = map(hygro0,400,1023,0,100); delay(100);

if (hygro0<30){
digitalWrite(relay0Pin, HIGH); delay(100);
}

if (hygro0>=70){
digitalWrite(relay0Pin, LOW); delay(100);
}

Serial.print("Soil humidity 0: "); Serial.print(hygro0);
Serial.println("%");
}

Το πρόγραμμα ενεργοποιεί τον κινητήρα όταν η υγρασία του εδάφους είναι μικρότερη από 30%. Όταν η υγρασία γίνει μεγαλύτερη από 70%, ο κινητήρας απενεργοποιείται.

Ξεκινάμε την προσομοίωση του κυκλώματος στο TinkerCAD.


Επιλέγουμε τον αισθητήρα ανίχνευσης της
υγρασίας του εδάφους στο χώρο σχεδίασης και μεταβάλλουμε τη θέση του δρομέα. Ελέγχουμε τη
σωστή εκτέλεση του προγράμματος παρατηρώντας την ενεργοποίηση και την απενεργοποίηση του κινητήρα.

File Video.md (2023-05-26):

Το βίντεο με την παρουσίαση του συστήματος αυτόματου ποτίσματος βρίσκεται στο κανάλι της ομάδας 2GM_Roboteam στο Youtube: https://youtu.be/hjsee6gfc14

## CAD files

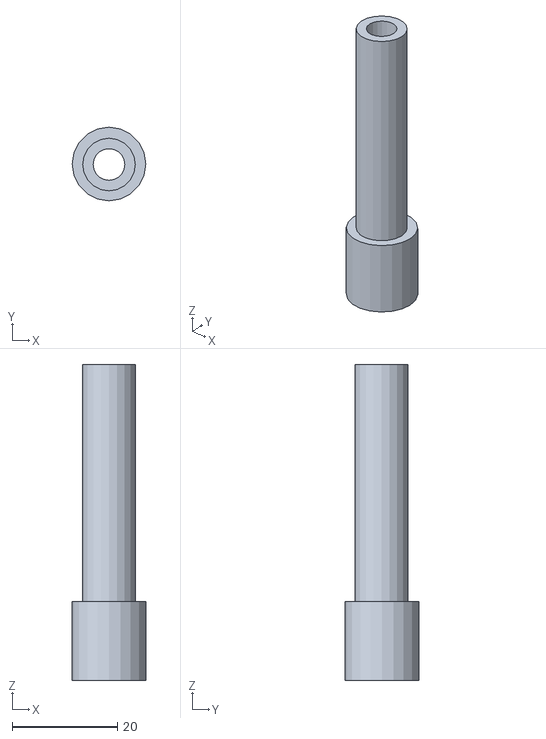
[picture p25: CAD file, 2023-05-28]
Stl/Gutter pipe1.stl
14.0 x 14.0 x 60.0

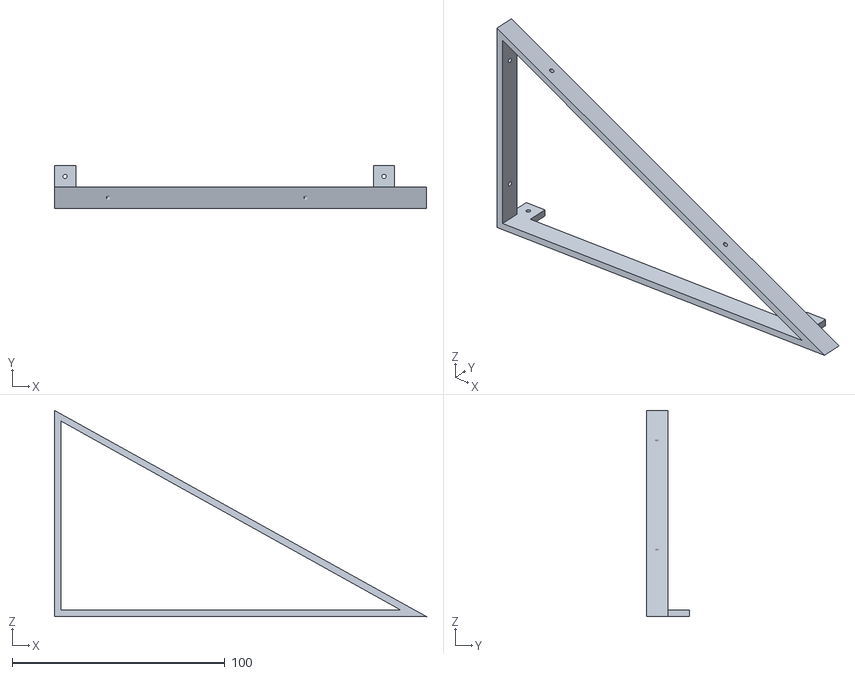
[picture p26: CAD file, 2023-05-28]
Stl/Roof base1.stl
175.0 x 20.0 x 97.0

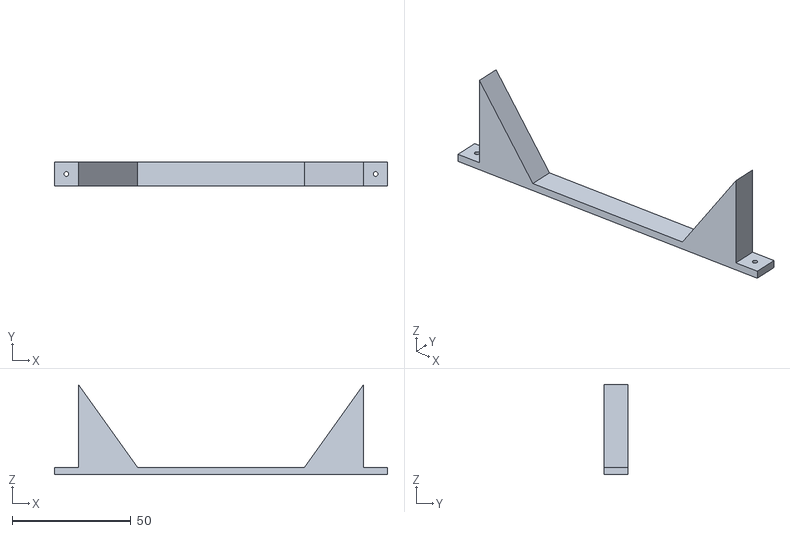
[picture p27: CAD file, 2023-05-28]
Stl/Tank Base.stl
140.0 x 10.0 x 38.0

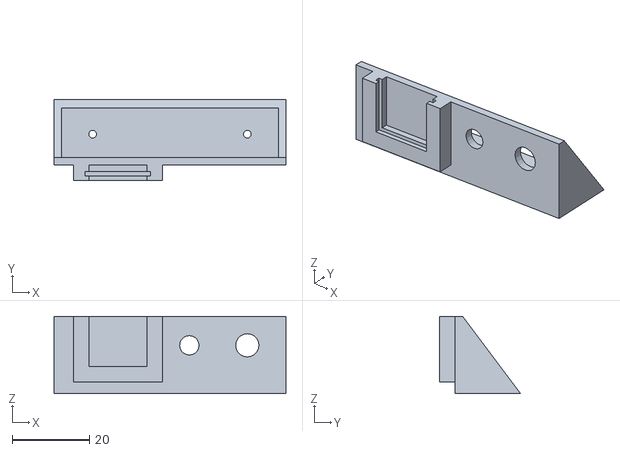
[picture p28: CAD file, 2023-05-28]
Stl/SwitchBase.stl
60.0 x 21.0 x 20.0

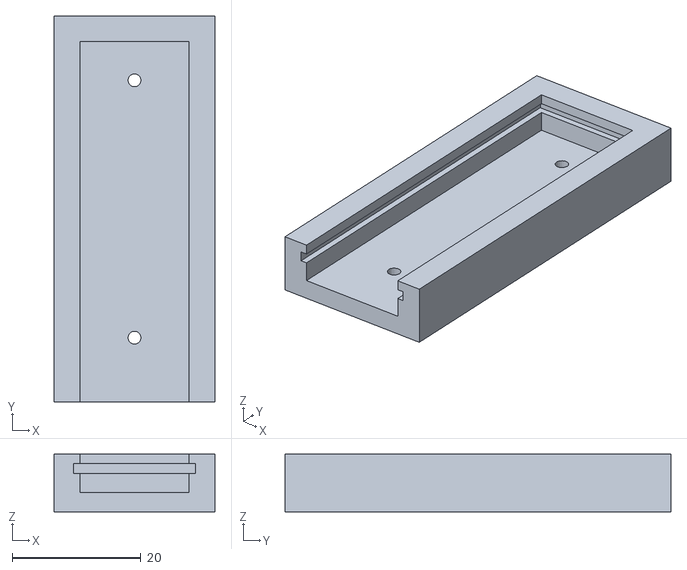
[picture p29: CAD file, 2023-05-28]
Stl/Relay base.stl
25.0 x 60.0 x 9.00

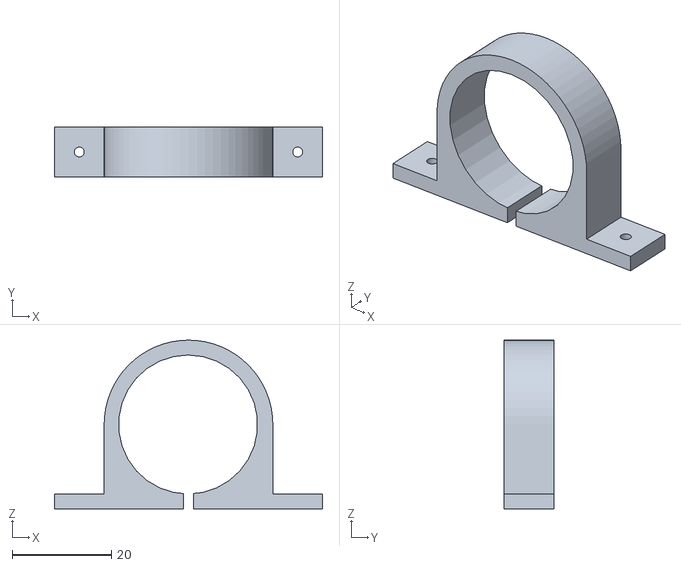
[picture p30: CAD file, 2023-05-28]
Stl/Pump base.stl
54.0 x 10.0 x 34.0

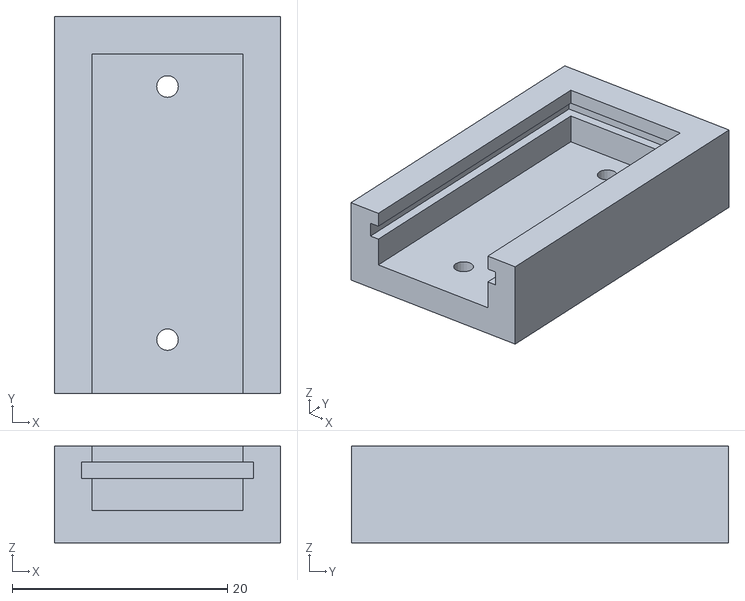
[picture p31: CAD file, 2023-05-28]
Stl/Hygrometer base.stl
21.0 x 35.0 x 9.00

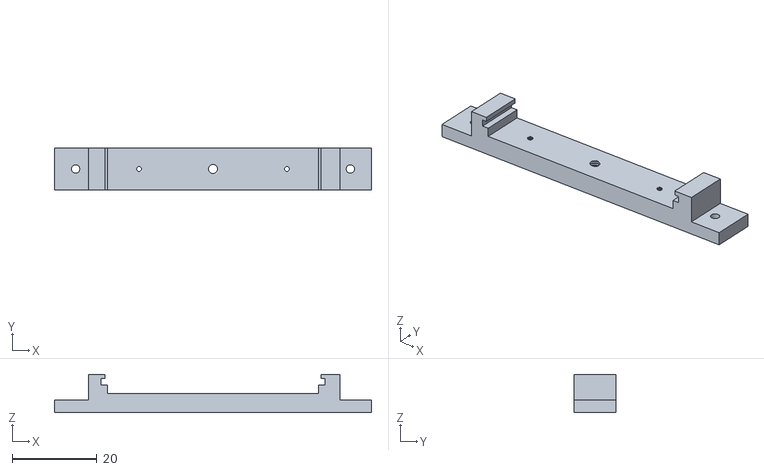
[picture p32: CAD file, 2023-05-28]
Stl/Breadboard base.stl
75.0 x 10.0 x 9.00

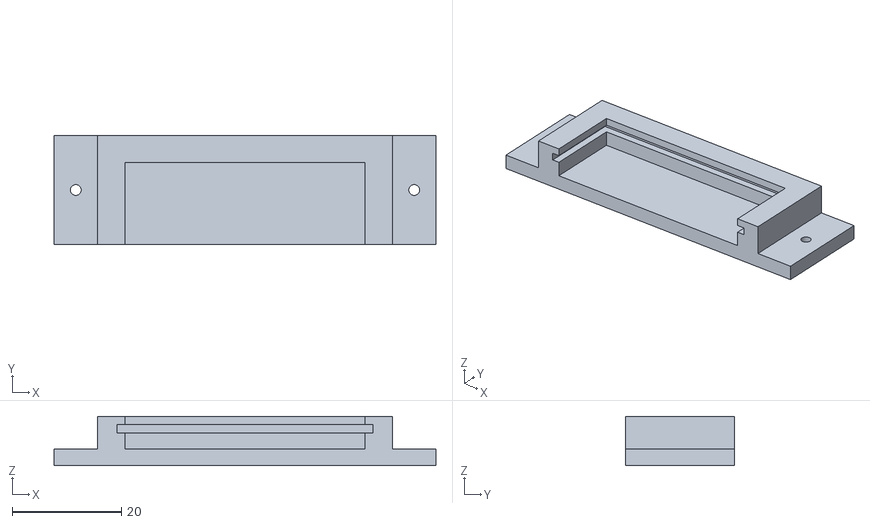
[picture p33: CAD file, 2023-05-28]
Stl/Ultrasonic base.stl
70.0 x 20.0 x 9.00

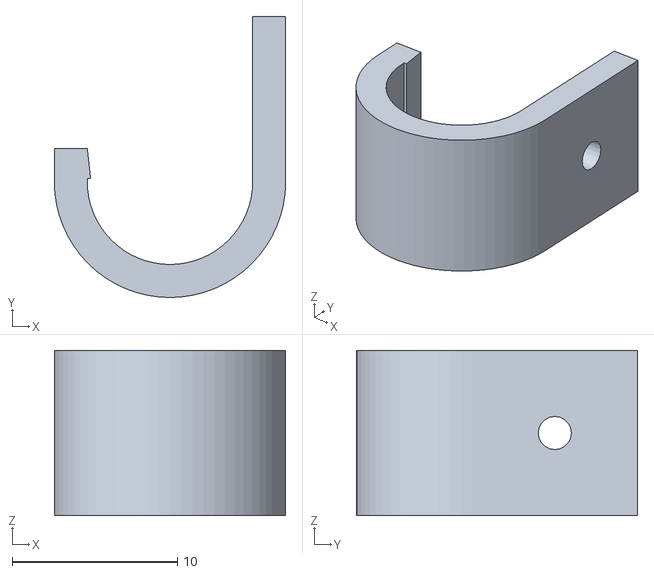
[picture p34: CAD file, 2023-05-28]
Stl/Gutter base.stl
14.0 x 17.0 x 10.0

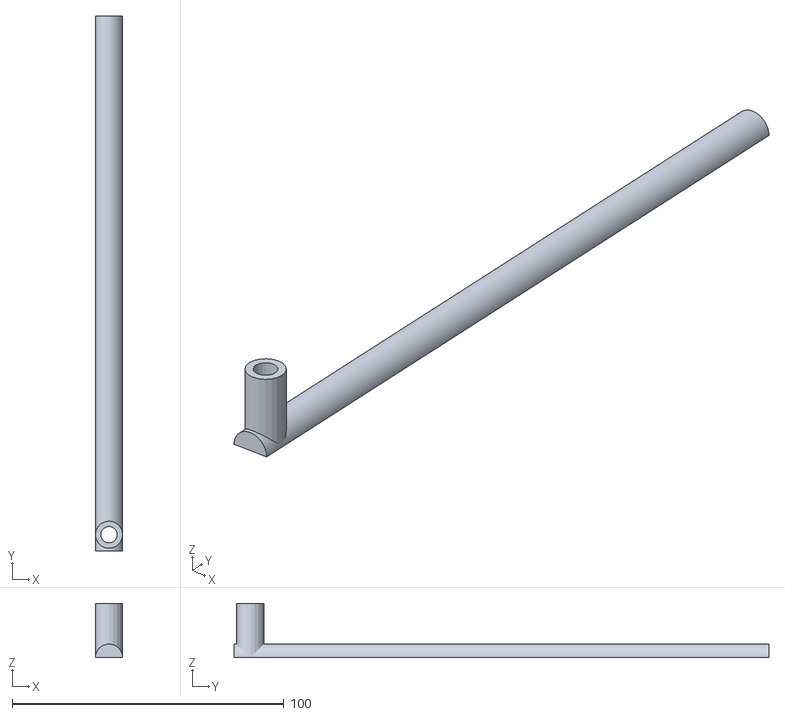
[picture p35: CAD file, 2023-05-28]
Stl/Gutter.stl
10.0 x 197.0 x 20.0

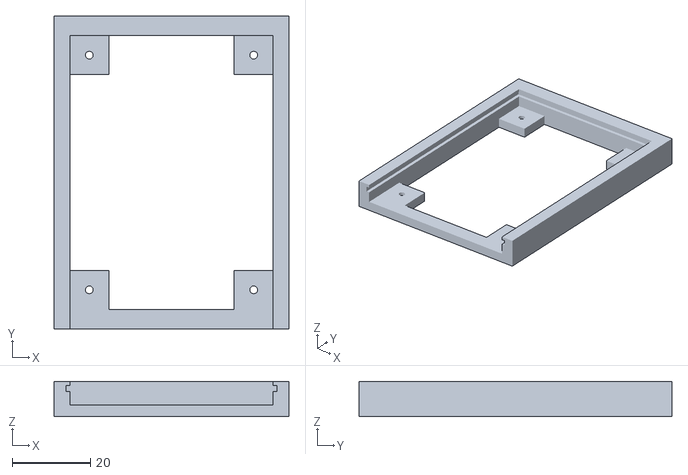
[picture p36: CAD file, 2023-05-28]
Stl/Arduino base.stl
60.0 x 80.0 x 9.00

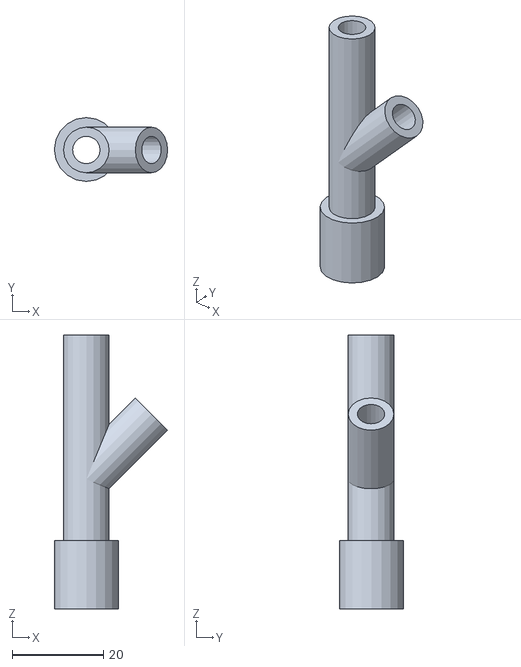
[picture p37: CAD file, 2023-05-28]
Stl/Gutter pipe2.stl
24.8 x 14.0 x 60.0

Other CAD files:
Stl/Roof base2.stl
